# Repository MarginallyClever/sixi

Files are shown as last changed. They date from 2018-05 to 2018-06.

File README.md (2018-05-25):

# Sixi Robot Arm

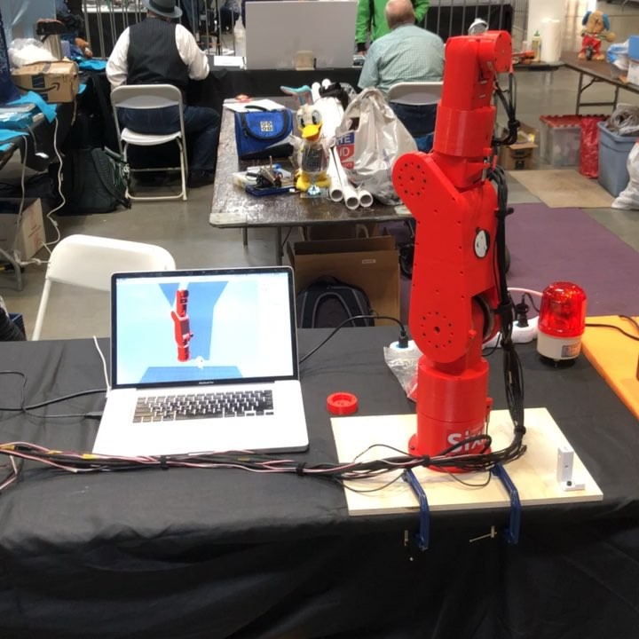
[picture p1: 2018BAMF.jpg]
Sixi robot arm at Bay Area Maker Fair 2018


Sixi is an open source industrial robot arm.  It is designed with six degrees of freedom and can hold 2kg at 50cm.

## Motivation

3D printers can print parts for themselves, but they cannot self-assemble.  The long goal of the Sixi is to build a machine that can assemble copies of itself.

When 3D printers were closed source, they started at $10k.  Makerbot and Prusa changed the game by bringing high quality open source 3D printers down to $2k.  Marginally Clever Robots, Ltd. aims to be the Prusa of robot arms.

## Ease

The Sixi has no epoxy because we like operations that can be undone.
The Sixi has no timing belts because they are annoying to keep tensioned.

All the 3D printable parts were produced on a Prusa MK2s at default settings (20% infill, 200um layer height).  Parts are carefully designed to have a minimum of support material cleaning.

## Links and Info

Sixi was designed in Fusion 360.  The design is publicly shared...

...as the last stable version: https://a360.co/2s9NEJI
...as the development version: http://a360.co/2pgpNaG

Marginally Clever uses our home made Robot Overlord app to simulate, drive, and test the Sixi robot arm.

https://github.com/MarginallyClever/Robot-Overlord-App

Marginally Clever uses Makelangelo Firmware in the Arduino compatible brain of the robot.

https://github.com/MarginallyClever/Makelangelo-firmware

## This repository

This repository contains:

* The STL files from the stable version
* Data sheet descriptions of the milled aluminum parts
* The bill of materials (BOM)
* A list of our commercial sources (In the BOM)
* Assembly instructions and animations _in progress_
* Usage instructions _soon_
* Wiring schematic _in progress_
* Issue tickets specifically related to the hardware

## Collaborate

We love collaborating!  Let's make great things happen together.

You can reach us online at http://marginallyclever.com/

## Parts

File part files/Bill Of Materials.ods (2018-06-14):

Qty | Name | Source | Part number at source |  | URI
1 | RUMBA 3D printer controller | reprapdiscount.com | RUMBA Basic Board |  | http://www.reprapdiscount.com/electronics/33-rumba-basic-board.html
2 | 2/4 phase Nema 23 Stepper Motor Driver 24-50VDC 1.5A-4.5A 256 Microstep M542T | omc-stepperonline | M542T |  | https://www.omc-stepperonline.com/nema-23-stepper-motor-drive-24-50vdc-15a-45a-256-microstep-m542t-m542t.html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
2 | TB6560 3A Driver Board | sainsmart.com | 101-60-190 |  | https://www.sainsmart.com/products/3a-single-axis-cnc-router-stepper-motor-driver-board-tb6560
2 | a4988 stepper driver | pololu.com | 1182 |  | https://www.pololu.com/product/1182
4 | bearing 6014-2RS1 70x110x20 | vxb.com | 6014-2RS1 |  | https://www.vxb.com/6014-2RS1-Bore-Dia-70mm-OD-110mm-Width-20mm-p/6014-2rs1.htm
4 | bearing 61812-2RS1 60x78x10 | vxb.com | 61812-2RS1 |  | https://www.vxb.com/61812-2RS1-Bore-Dia-60mm-OD-78mm-Width-10mm-p/61812-2rs1.htm
3 | bearing 6806-2RZ 30x42x7 | vxb.com | 6806-2RSBEARING |  | https://www.vxb.com/6806-2RS-Bearing-Deep-Groove-6806-2RS-p/6806-2rsbearing.htm
1 | bearing MR6700-ZZ-W3 15x10x4 | vxb.com | MR6700-ZZ-W3 |  | https://www.vxb.com/MR6700-ZZ-W3-Bore-Dia-10mm-OD-15mm-Width-3mm-p/mr6700-zz-w3.htm
 |  |  | Paste the following into McMaster-carr’s “paste products and quantities” field |  | https://www.mcmaster.com/#orders
6 | m2 nylock nut 93625A101 | Mcmaster-carr | 93625A101 | 1
8 | m2 washer 90965A110 | Mcmaster-carr | 90965A110 | 1
4 | m2x25 socket head cap screw 91292A032 | Mcmaster-carr | 91292A032 | 1
2 | m2x30 socket head cap screw 91292A034 | Mcmaster-carr | 91292A034 | 1
4 | m2x6 socket head cap screw 91290A013 | Mcmaster-carr | 91290A013 | 1
8 | m3 hex nut 92497A200 | Mcmaster-carr | 92497A200 | 1
14 | m3 nylock 93625A100 | Mcmaster-carr | 93625A100 | 1
4 | m3 press nut 97648A410 | Mcmaster-carr | 97648A410 | 1
1 | m3x14 socket head cap screw 91290A119 | Mcmaster-carr | 91290A119 | 1
4 | m3x16 socket cap head screw 91290A120 | Mcmaster-carr | 91290A120 | 1
10 | m3x20 socket head cap screw 91290A123 | Mcmaster-carr | 91290A123 | 1
18 | m3x22 socket head cap screw 91290A124 | Mcmaster-carr | 91290A124 | 1
12 | m3x24 socket head cap screw 91290A125 | Mcmaster-carr | 91290A125 | 1
32 | m3x35 hex head cap screw 91290A135 | Mcmaster-carr | 91290A135 | 1
26 | m3x45 socket head cap screw 91290A145 | Mcmaster-carr | 91290A145 | 1
36 | m3x6x20 hex standoff 95947A054 | Mcmaster-carr | 95947A054 | 36
1 | m3x6 set screw Steel Cup-Point 91390A100 | Mcmaster-carr | 91390A100 | 1
51 | m3x8 socket head cap screw 91290A113 | Mcmaster-carr | 91290A113 | 1
4 | m4 nut 92497A250 | Mcmaster-carr | 92497A250 | 1
4 | m4x14 socket head cap screw 91290A150 | Mcmaster-carr | 91290A150 | 1
4 | m4x20 socket head cap screw 91274A121 | Mcmaster-carr | 91274A121 | 1
4 | M5 nut 92497A300 | Mcmaster-carr | 92497A300 | 1
8 | m5x20 socket head cap screw 91290A238 | Mcmaster-carr | 91290A238 | 1
4 | m5x45 hex head cap screw 91290A197 | Mcmaster-carr | 91290A197 | 1
1 | NEMA14 with 19:1 planetary gearbox | omc-stepperonline | 14HS13-0804S-PG19 |  | https://www.omc-stepperonline.com/geared-stepper-motor/nema-14-stepper-motor-bipolar-l33mm-w-gear-raio-191-planetary-gearbox-14hs13-0804s-pg19.html
2 | NEMA17 with 15:1 planetary gearbox | omc-stepperonline | 17HS15-1684S-HG15 |  | https://www.omc-stepperonline.com/geared-stepper-motor/nema-17-stepper-motor-l39mm-gear-raio-151-high-precision-planetary-gearbox-17hs15-1684s-hg15.html
2 | NEMA23 with 47:1 planetary gearbox | omc-stepperonline | 23HS30-2804S-PG47 |  | https://www.omc-stepperonline.com/geared-stepper-motor/nema-23-stepper-motor-bipolar-l76mm-w-gear-raio-471-planetary-gearbox-23hs30-2804s-pg47.html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
1 | NEMA8 90:1 planetary gearbox | omc-stepperonline | 8HS15-0604S-PG90 |  | https://www.omc-stepperonline.com/geared-stepper-motor/nema-8-stepper-motor-bipolar-l38mm-w-gear-raio-901-planetary-gearbox-8hs15-0604s-pg90.html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
6 | PINDA probe XAGIPS8X4-5V | www.xagyl3d.com | XAGIPS8X4-5V |  | https://www.xagyl3d.com/oc2/XAGIPS8X4-5V?search=XAGIPS8X4-5V
2 | shaft key 3x14 | comes with stepper motor from stepperonline.com
2 | shaft key 4x16 | comes with stepper motor from stepperonline.com
1 | In Win CE052 Micro-ATX/Mini-ITX Case with 300W 80+ Gold PSU - Black | aliexpress
2 | large adapter | milled from aluminum
2 | small adapter | milled from aluminum
1 | handHead | 3d printed
1 | handTail | 3d printed
1 | wristHead | 3d printed
1 | wristTail | 3d printed
1 | wristSpacerIdlerSide | 3d printed
1 | wristBodyGearSide | 3d printed
1 | wristSpaderGearSide | 3d printed
1 | wristBearingMountGearSide | 3d printed
1 | wristBodyIdlerSide | 3d printed
1 | wristBearingMountIdlerSide | 3d printed
1 | forearmBottom | 3d printed
1 | forearmMotor | 3d printed
1 | forearmTop | 3d printed
1 | forearmPulley | 3d printed
1 | forearmPulleyA | 3d printed
1 | forearmSensorMount | 3d printed
1 | forearmPulleyB | 3d printed
1 | forearmCover | 3d printed
1 | elbowTorso | 3d printed
1 | elbowHead | 3d printed
1 | elbowLeftFoot | 3d printed
1 | elbowNeck | 3d printed
1 | elbowWaist | 3d printed
1 | elbowRightFoot | 3d printed
1 | bicepLeftLeg | 3d printed
1 | bicepLeftArm | 3d printed
1 | bicepRightLeg | 3d printed
1 | bicepRightArm | 3d printed
1 | bicepCore | 3d printed
1 | shoulderWaist | 3d printed
1 | shoulderRight | 3d printed
1 | shoulderLeft | 3d printed
1 | shoulderBottom | 3d printed
1 | anchorTop | 3d printed
1 | anchorHips | 3d printed
1 | anchorTorso | 3d printed
1 | anchorBottom | 3d printed
1 | anchorFloor | 3d printed

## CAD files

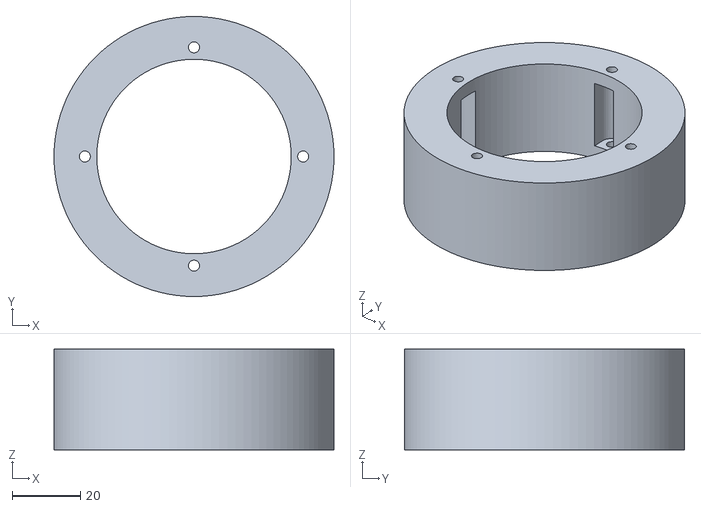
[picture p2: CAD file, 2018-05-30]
part files/anchor/anchorTorso.stl
82.1 x 82.1 x 29.5

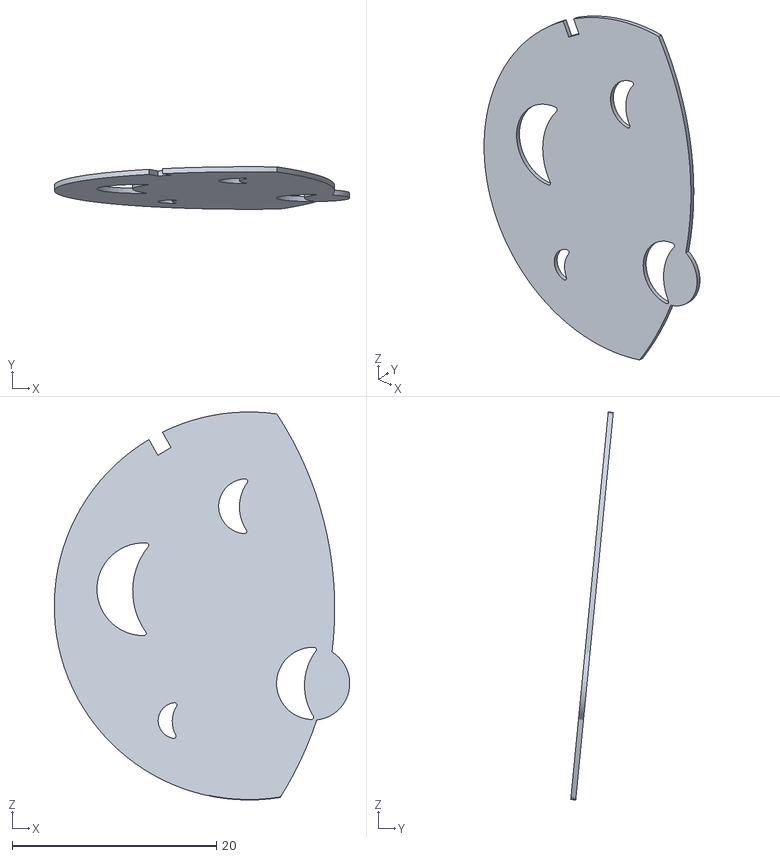
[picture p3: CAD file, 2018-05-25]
part files/bicep/logoSmallWhite.stl
28.9 x 4.17 x 38.0

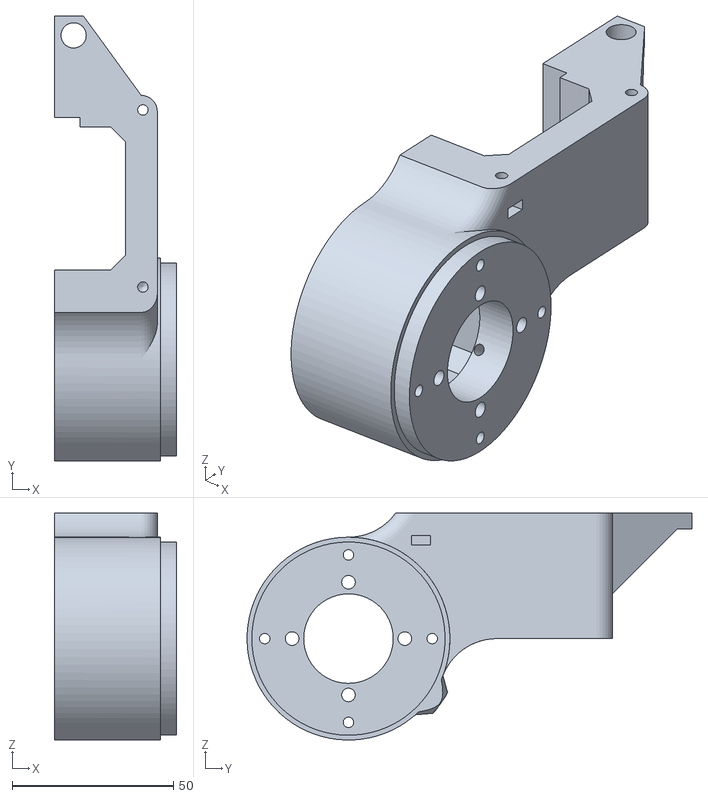
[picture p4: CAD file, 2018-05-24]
part files/elbow/elbowRightFoot.stl
38.0 x 138.1 x 70.5

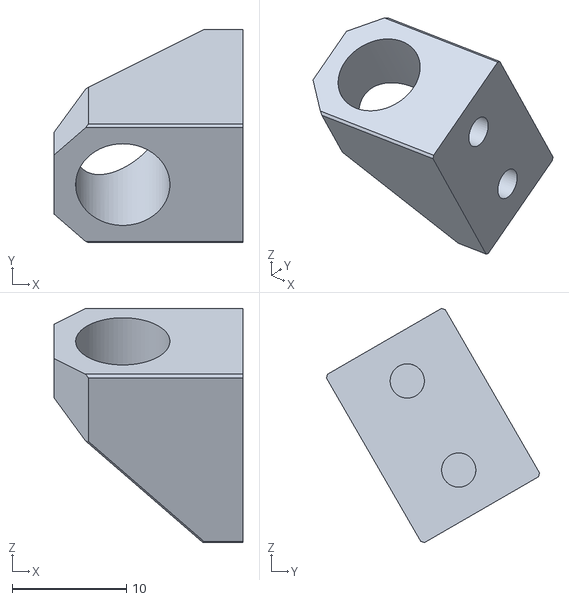
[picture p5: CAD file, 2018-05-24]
part files/forearm/forearmSensorMount.stl
16.5 x 18.6 x 20.5

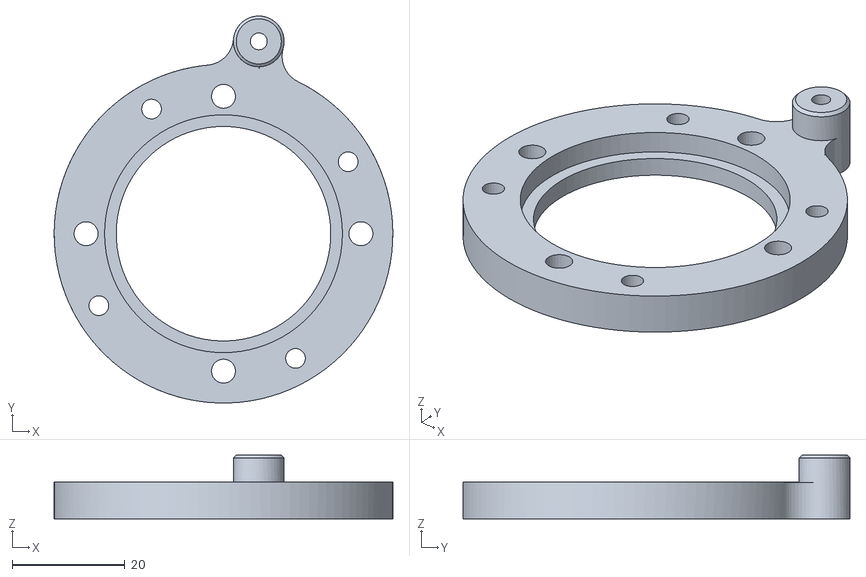
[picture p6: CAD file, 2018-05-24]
part files/hand/handTail.stl
60.0 x 68.6 x 11.3

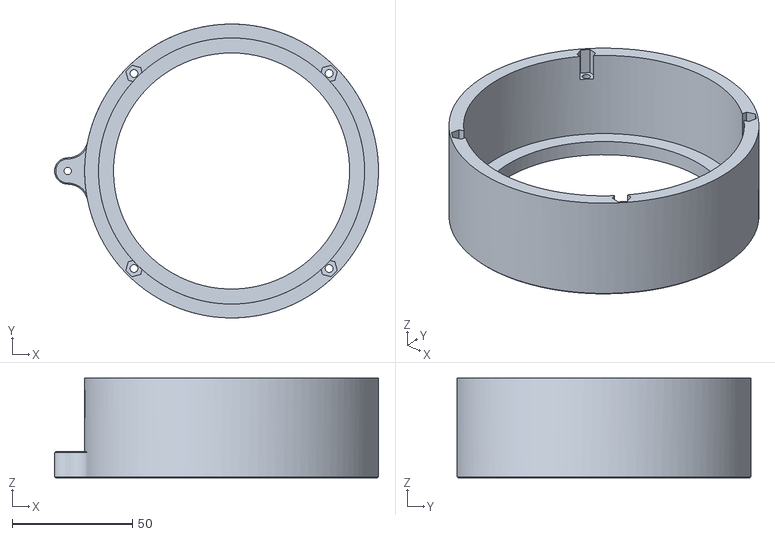
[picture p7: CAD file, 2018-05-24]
part files/shoulder/shoulderBottom.stl
134.5 x 122.0 x 41.5

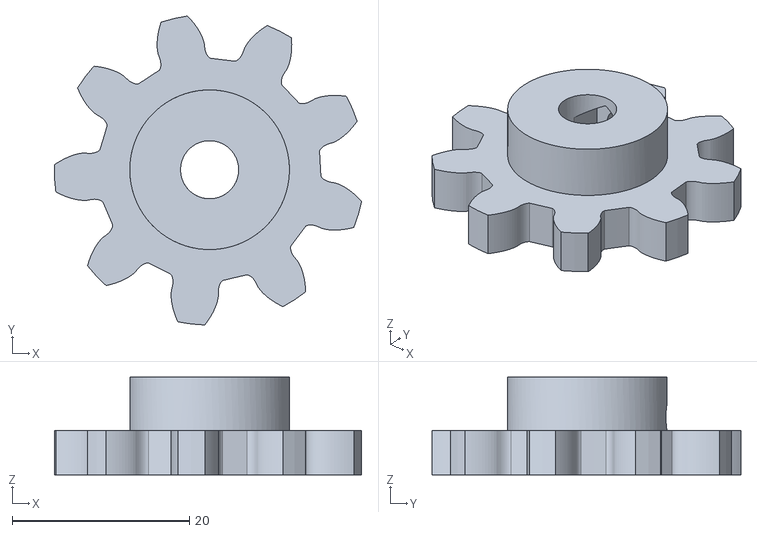
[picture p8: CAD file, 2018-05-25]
part files/wrist/wristGearPinion.stl
34.6 x 34.8 x 11.0

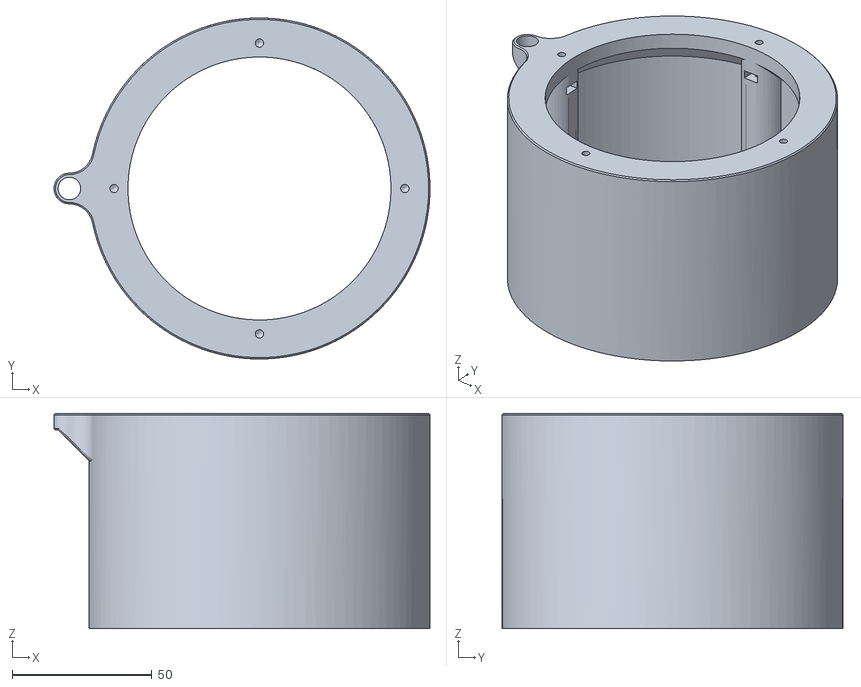
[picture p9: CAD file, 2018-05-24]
part files/anchor/anchorBottom.stl
134.5 x 122.0 x 77.0

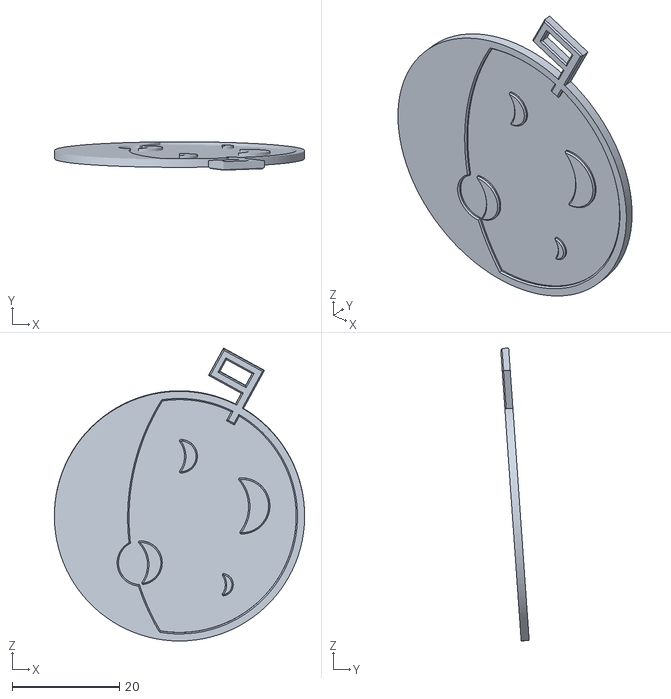
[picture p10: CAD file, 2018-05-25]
part files/bicep/logoBigBlack.stl
46.6 x 5.29 x 54.5

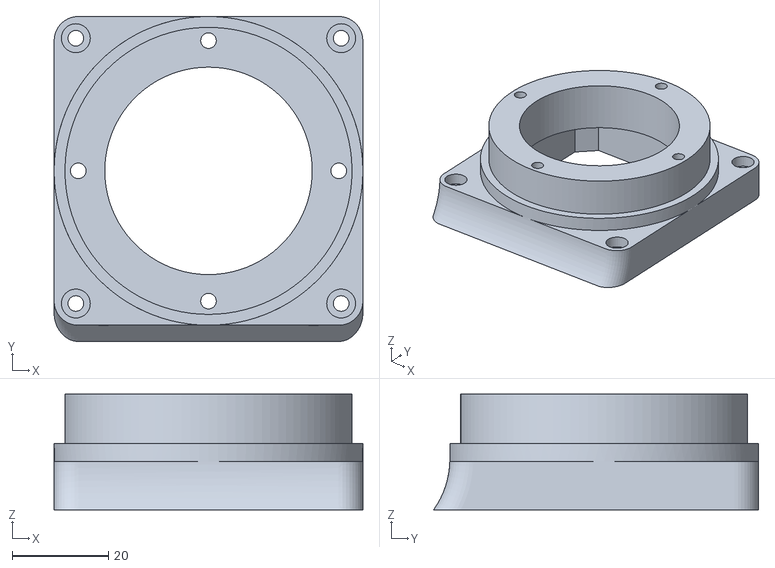
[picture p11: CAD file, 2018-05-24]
part files/elbow/elbowWaist.stl
64.0 x 67.4 x 24.0

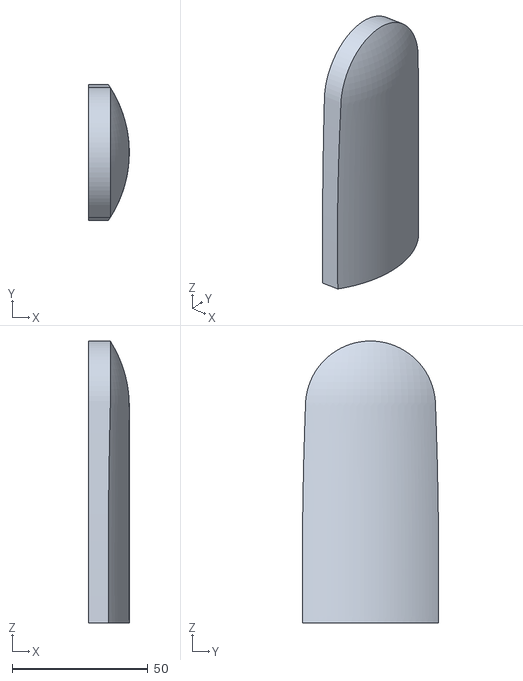
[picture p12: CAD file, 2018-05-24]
part files/forearm/forearmCover.stl
15.0 x 50.3 x 104.0

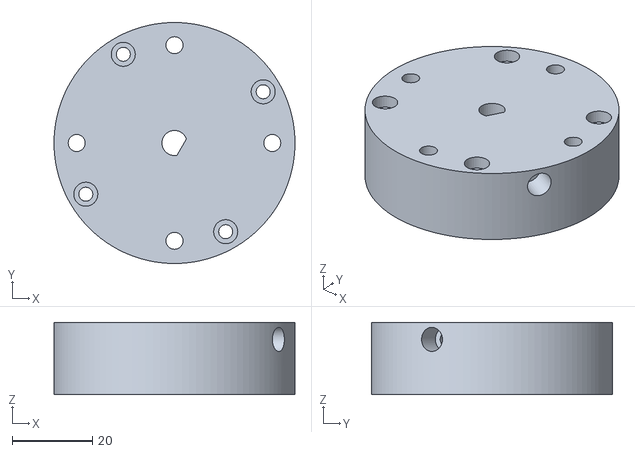
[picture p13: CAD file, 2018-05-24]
part files/hand/handHead.stl
60.0 x 60.0 x 18.0

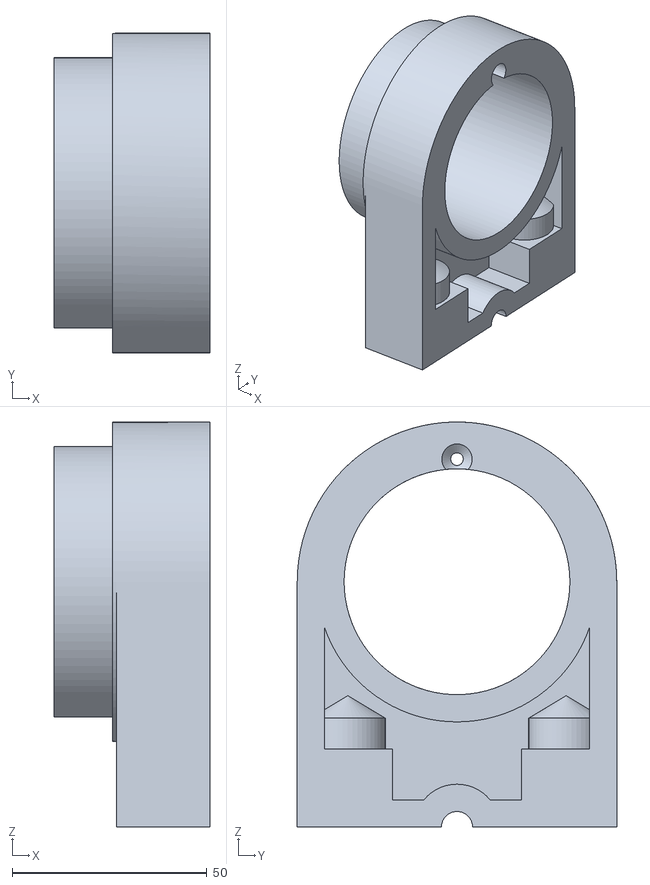
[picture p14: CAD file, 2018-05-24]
part files/shoulder/shoulderRight.stl
40.0 x 82.1 x 104.0

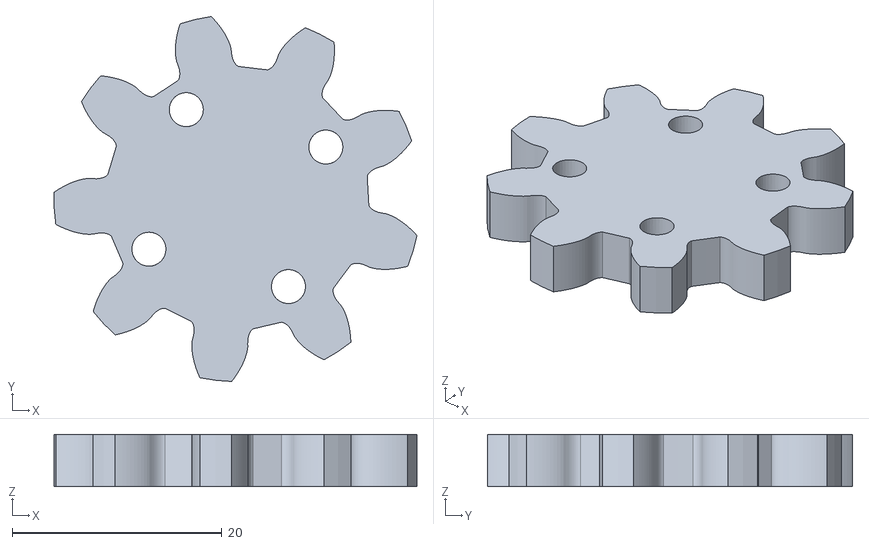
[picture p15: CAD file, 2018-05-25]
part files/wrist/wristGear.stl
34.6 x 34.8 x 5.00

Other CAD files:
part files/anchor/anchorFloor.stl
part files/bicep/logoSmallBlack.stl
part files/elbow/elbowLeftFoot.stl
part files/forearm/forearmPulleyA.stl
part files/anchor/anchorHips.stl
part files/anchor/anchorTop.stl
part files/bicep/bicepCore.stl
part files/bicep/bicepLeftArm.stl
part files/bicep/bicepLeftLeg.stl
part files/bicep/bicepRightArm.stl
part files/bicep/bicepRightLeg.stl
part files/bicep/logoBigWhite.stl
part files/elbow/elbowHead.stl
part files/elbow/elbowNeck.stl
part files/elbow/elbowTorso.stl
part files/forearm/forearmBottom.stl
part files/forearm/forearmMotor.stl
part files/forearm/forearmPulley.stl
part files/forearm/forearmPulleyB.stl
part files/forearm/forearmTop.stl
part files/shoulder/shoulderLeft.stl
part files/shoulder/shoulderWaist.stl
part files/wrist/wristBearingMountGearSide.stl
part files/wrist/wristBearingMountIdlerSide.stl
part files/wrist/wristBodyGearSide.stl
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

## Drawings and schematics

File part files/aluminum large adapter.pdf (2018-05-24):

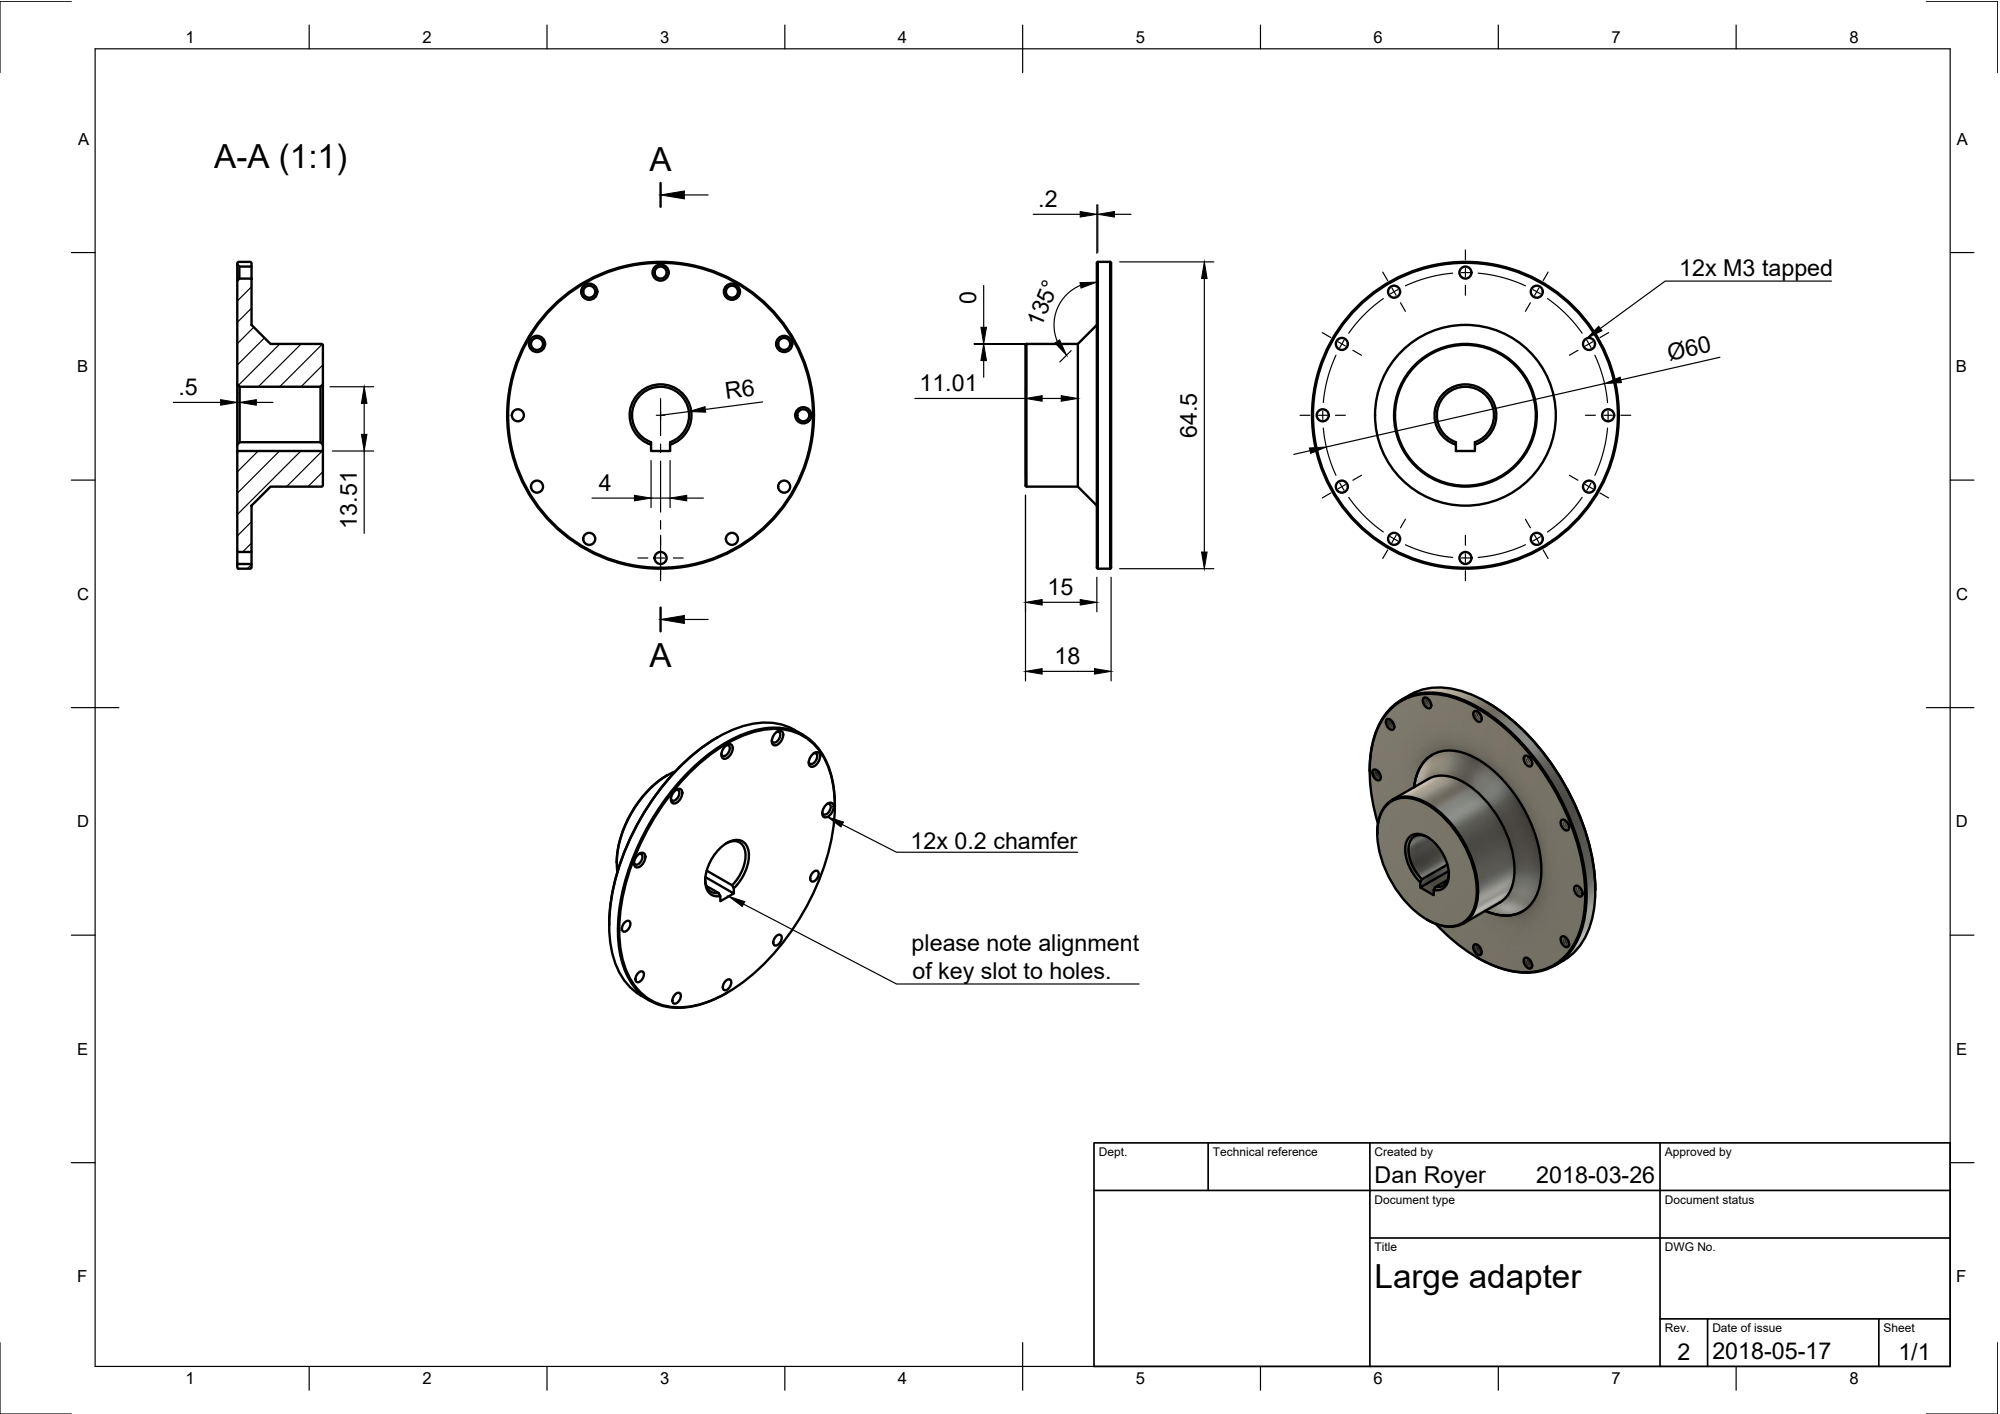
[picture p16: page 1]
12x M3 tapped 64.5; 12x 0.2 chamfer

please note alignment
of key slot to holes.

Dept. | Technical reference | Created by Dan Royer 2018-03-26 | Approved by

Document type | Document status

Title Large adapter | DWG No.

Rev. 2 | Date of issue 2018-05-17 | Sheet 1/1

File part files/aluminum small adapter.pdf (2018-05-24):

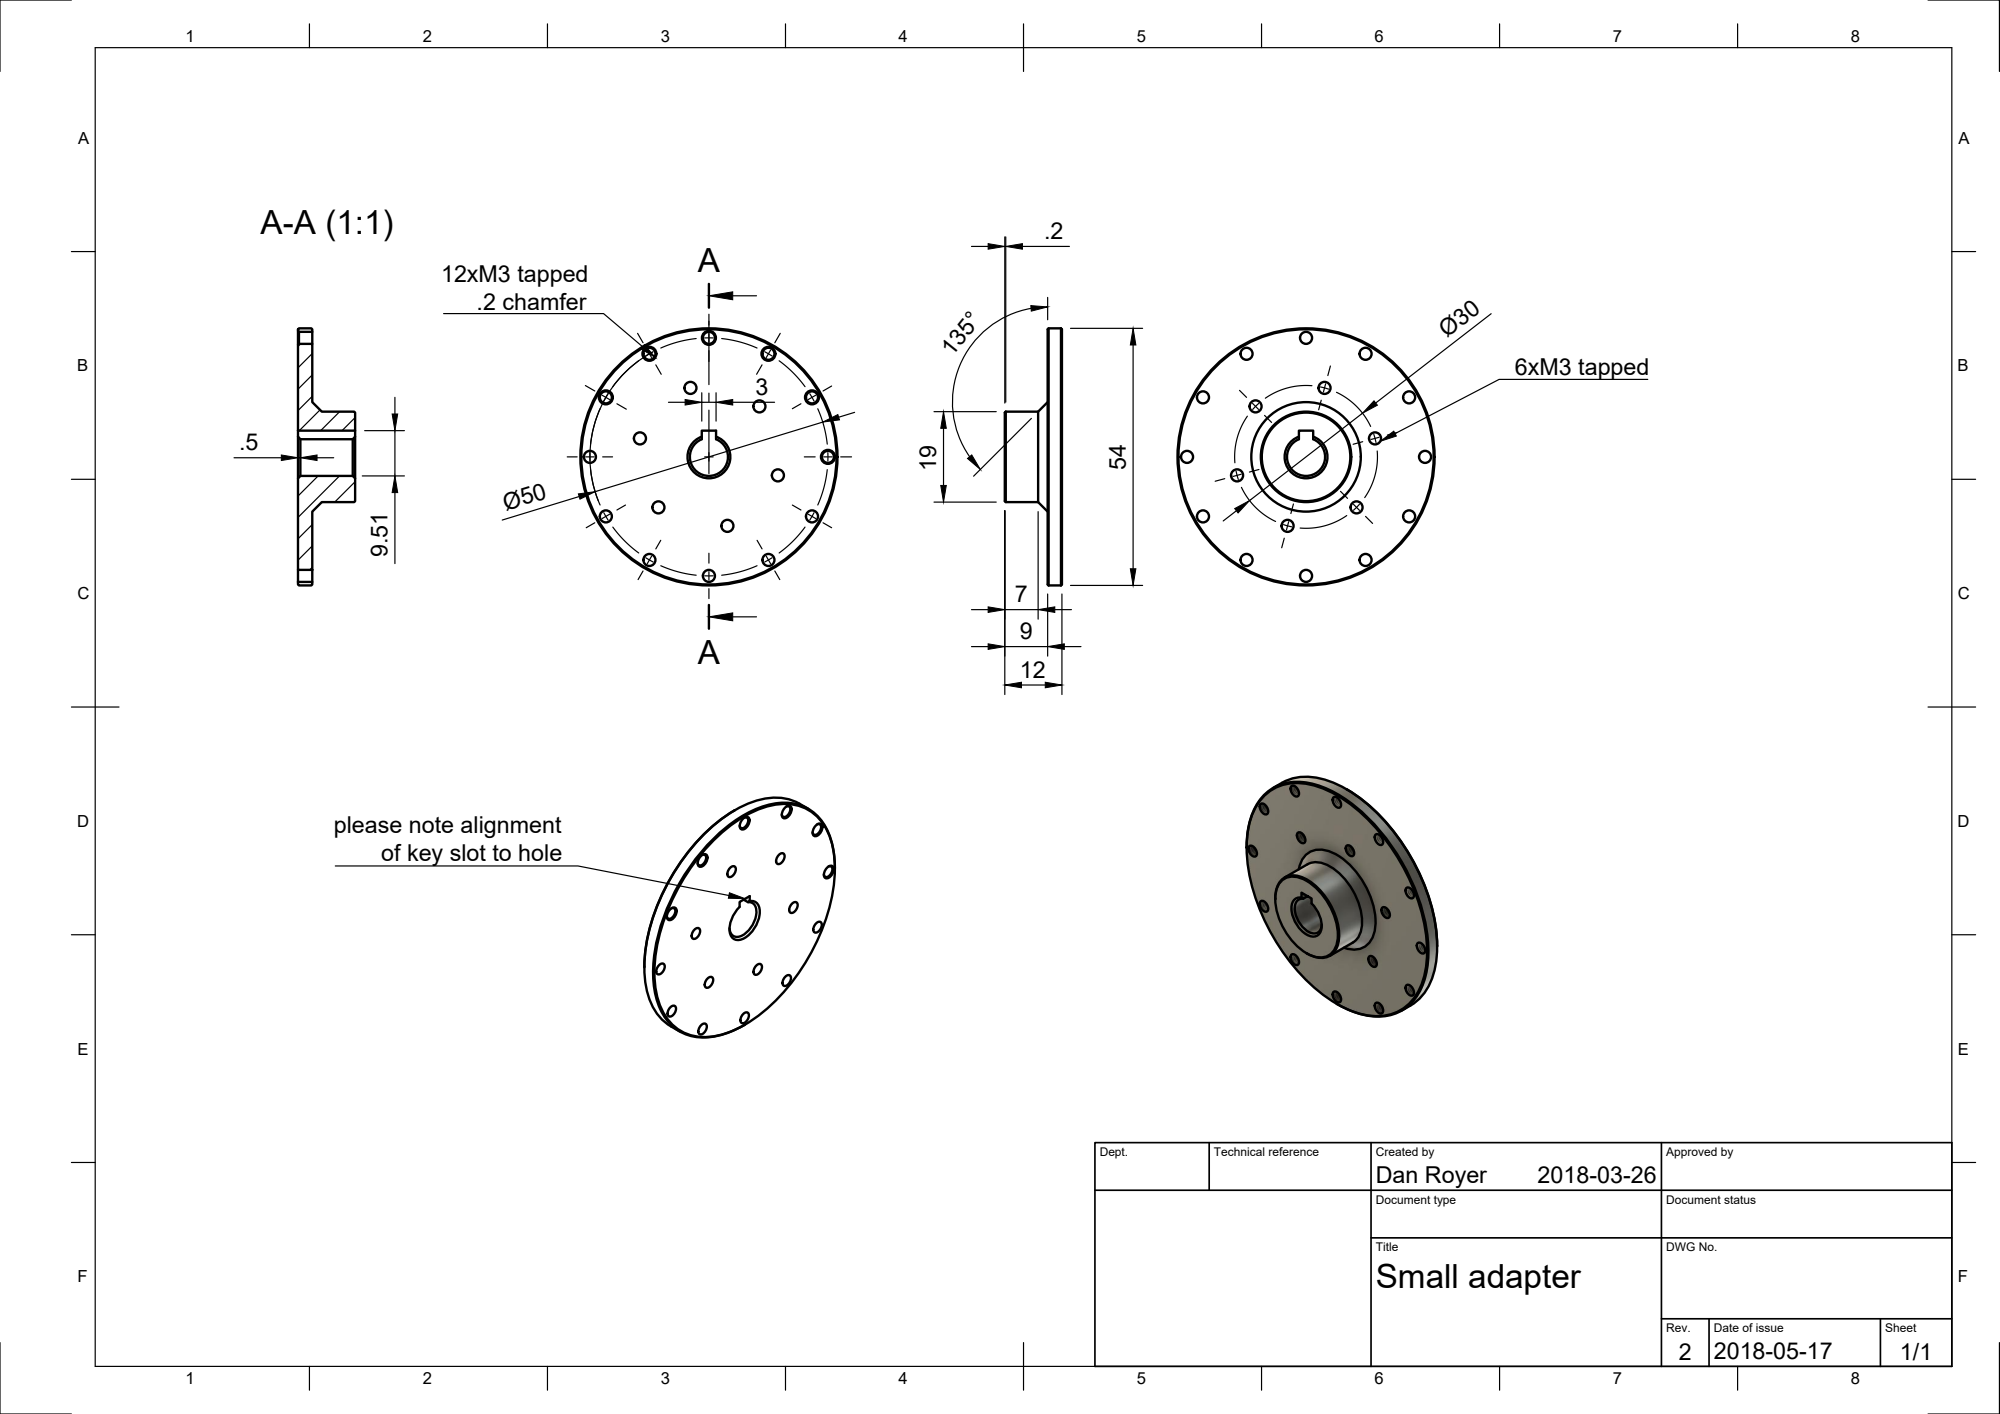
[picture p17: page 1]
6xM3 tapped; 12xM3 tapped .2 chamfer

please note alignment
of key slot to hole

Dept. | Technical reference | Created by Dan Royer 2018-03-26 | Approved by

Document type | Document status

Title Small adapter | DWG No.

Rev. 2 | Date of issue 2018-05-17 | Sheet 1/1

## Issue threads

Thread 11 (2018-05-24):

Firmware - add Inverse Kinematics

i-make-robots, 2018-05-24:
copy from Robot Overlord where it's already solved.

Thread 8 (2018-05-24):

Automatic Tool Changer

i-make-robots, 2018-05-24:
Fits on existing wrist.  allows arm to release one tool and pick up another, provided tools have correct mating interface.

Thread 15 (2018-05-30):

Solve loose screws in anchor

i-make-robots, 2018-05-30:
disassemble anchor and find out why upward facing screws are loose.

i-make-robots, 2018-05-30:
Looks like I left two metal spacers out of the assembly?  Nothing holding the screws in place!
Also little preventing the parts from rotating - except the screws.

i-make-robots, 2018-05-30:
missing parts ordered from mcmaster.

Closed 2018-05-30.

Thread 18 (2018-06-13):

Part numbers in BOM for purchased components

TELunus, 2018-06-13:
For purchased components part number at source should be a separate column in the bill of materials.

TELunus, 2018-06-13:
@i-make-robots
I'm not sure whether the item `NEMA23 with 47:1 planetary gearbox ` from `stepperonline.com` is supposed to be [the L=56mm one](https://www.omc-stepperonline.com/economy-planetary-gearbox/nema-23-stepper-motor-bipolar-l56mm-w-gear-raio-471-planetary-gearbox-23hs22-2804s-pg47.html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), or [ the L=76mm one](https://www.omc-stepperonline.com/economy-planetary-gearbox/nema-23-stepper-motor-bipolar-l76mm-w-gear-raio-471-planetary-gearbox-23hs30-2804s-pg47.html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)

TELunus, 2018-06-13:
There's a similar issue with the `NEMA8 90:1 planetary gearbox `, it could be L=30 or L=38.

TELunus, 2018-06-13:
vxb.com doesn't seem to have a `bearing 6806-2RZ 30x42x7`, but they've got a bunch of other 30x42x7 bearings that are variations on 6806-2RS.  See http://www.vxb.com/SearchResults.asp?Search=6806-2RZ

i-make-robots, 2018-06-13:
commit cca7d3f

Closed 2018-06-13.

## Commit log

2018-05-24 renamed folder for clarity
    [anchorBottom.stl, anchorFloor.stl, anchorHips.stl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]
2018-05-24 reorganizing for clarity
    [anchorBottom.stl, anchorFloor.stl, anchorHips.stl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]
2018-05-25 added schematic file (empty)
    [sixi schematic.kicad_pcb, sixi schematic.sch]
2018-05-25 added more printable parts
    [logoBigBlack.stl, logoBigWhite.stl, logoSmallBlack.stl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]
2018-05-25 added off the shelf parts list (open office document)
    [off the shelf parts.ods]
2018-05-25 renamed bill of materials, added printed parts.
    [Bill Of Materials.ods, off the shelf parts.ods]
2018-05-26 update BOM
    [Bill Of Materials.ods]
2018-05-30 updated BOM and corrected STL file
    [Bill Of Materials.ods, anchorTorso.stl]
2018-05-30 one mcmaster carr part number wrong
    [Bill Of Materials.ods]
2018-06-13 update BOM (#18)
    added links to specific items.
    [Bill Of Materials.ods]
2018-06-13 seperated BOM fields for source, PN at source, and URI to purchase from source
    [Bill Of Materials.ods]
2019-04-20 Create belt length.ods
    [belt length.ods]
